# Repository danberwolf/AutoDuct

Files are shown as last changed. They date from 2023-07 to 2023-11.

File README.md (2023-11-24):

# AutoDuct: smart motorized air duct shutter
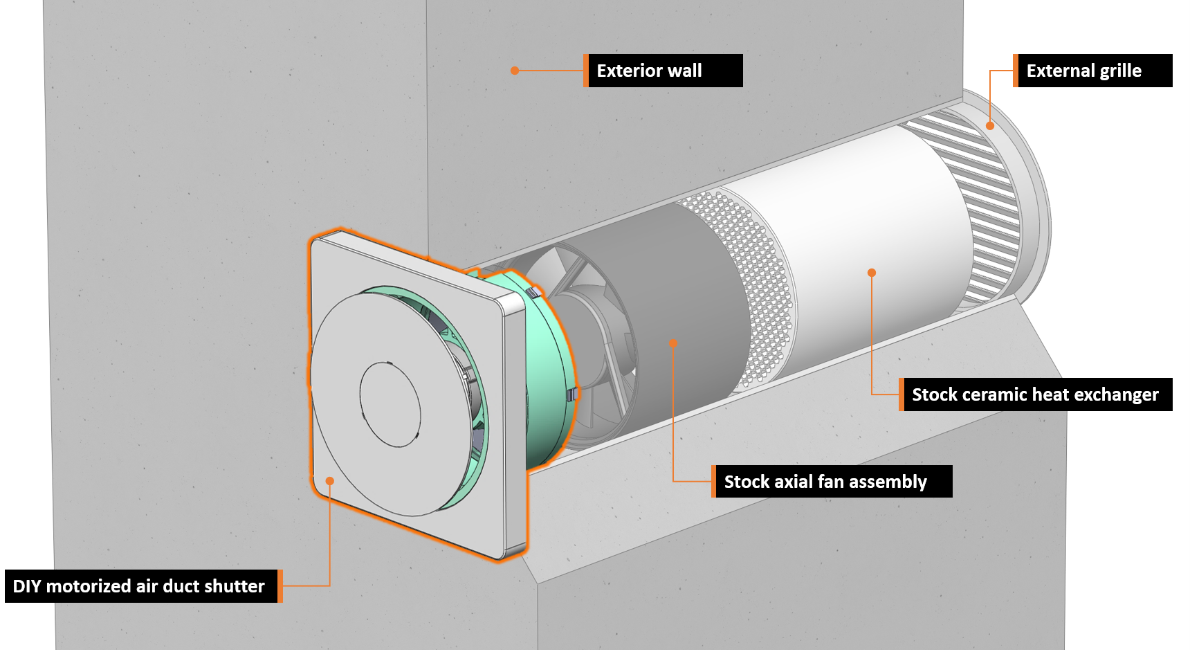
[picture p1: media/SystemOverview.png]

AutoDuct is a smart DIY air duct shutter for decentralized ventilation systems in residential buildings. Its main purpose is to automatically control airflow and block outside noise using a 3D-printed shutter system. This solves the problem of unintended air flow into the apartment during cold and windy days to increase comfort, maintain energy efficiency and reduce expenses for heating.
The integrated electronics of the air duct shutter assembly also gives full control of the ventilation system’s fan to enable features like flexible ventilation schedules and automatic humidity control. The Bluetooth low energy interface lets you control and configure the system via a mobile app. Multiple ventilation units can also be integrated into Apple HomeKit via a simple ESP32-powered BLE-to-Wifi-bridge.

# Mechanical Assembly

At the heart of this device is a mostly 3D-printed linear actuator which is used to open and close a shutter disc to prevent unwanted airflow. The 3D-printed leadscrew of the actuator is directly attached to a small brushed DC motor with an integrated gearbox.

Integrated into the encapsulated actuator unit two hall effect switches on a separate ring-shaped PCB are used to detect the end stop positions (open/close) of the shutter mechanism in combination with tiny magnets. The axial position of these magnets can be adjusted to compensate for mechanical tolerances in the assembly.

Note: the actuator unit does not use any additional (ball) bearings to keep the BOM simple and material cost low. Axial and radial forces are solely absorbed by the 3D-printed linear guides and the integrated bearings of the geared motor. This could potentially reduce longevity of the assembly but has not been an issue while testing multiple units over more than a year now. Use of silicone grease is highly recommended.



# Electronics

The electronics are based around a Microchip 32-bit microcontroller (PIC32MX), which might be a little bit overpowered for this project but was available from a previous project and has a neat footprint. The +3V3 rail is generated from the +12V bus by a step-down converter. The geared DC motor is driven by a dedicated H-bridge driver IC (DRV8801).

Behind the front cover of the assembly another small PCB is hidden. This PCB contains the Bluetooth low energy module (HM-17), a serial EEPROM, a real time clock (RTC) IC and a humidity and temperature sensor. User feedback is given via a white LED which shines through the 3D-printed enclosure and has brightness control via PWM.

# Firmware

The main processor of the device (PIC32MX150F128B) runs a super simple multitasking OS which takes care of these main tasks:

* monitoring of fan control PWM signal from the stock ventilation system control bus
* reading of temperature / humidity from SHT31 sensor
* generating the PWM control signal for connected fan
* motor control including end stop detection
* handle the BLE communication when the system is connected to the mobile app 

Depending on the selected operating mode, the device will perform the following actions:

* opening / closing the valve based on the detected fan control PWM signal
* automatically activating the fan based on schedule events or humidity thresholds
* react to remote control commands issued via the mobile app / BLE connection 

A custom bootloader was developed which enables over-the-air firmware updates via the Bluetooth low energy interface. 

# Project Video
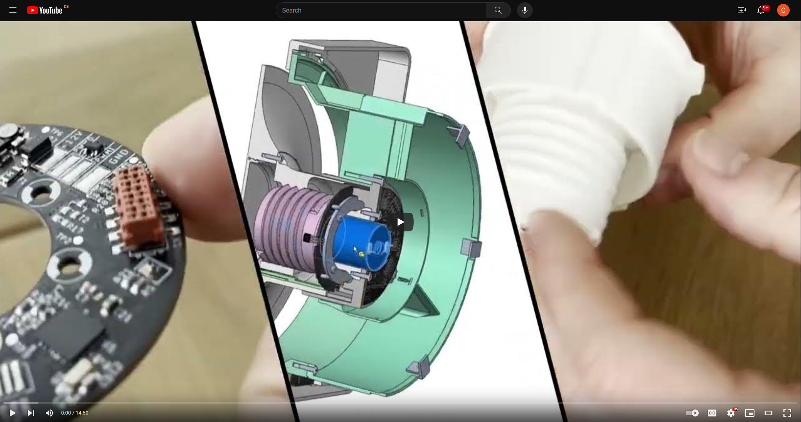
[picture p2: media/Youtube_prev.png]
Watch the video (https://youtu.be/yPaX_Ez_lKY)


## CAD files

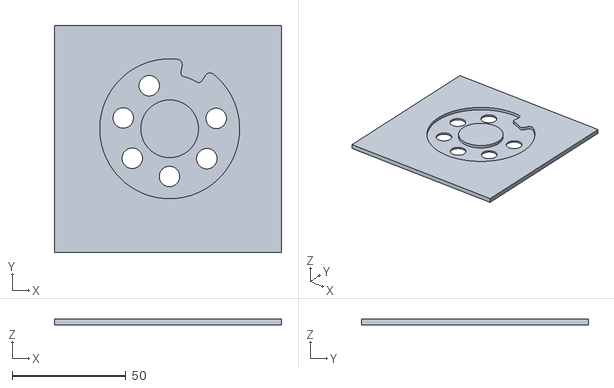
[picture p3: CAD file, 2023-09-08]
CAD/PCBassemblyTemplate.STL
100.0 x 100.0 x 2.50

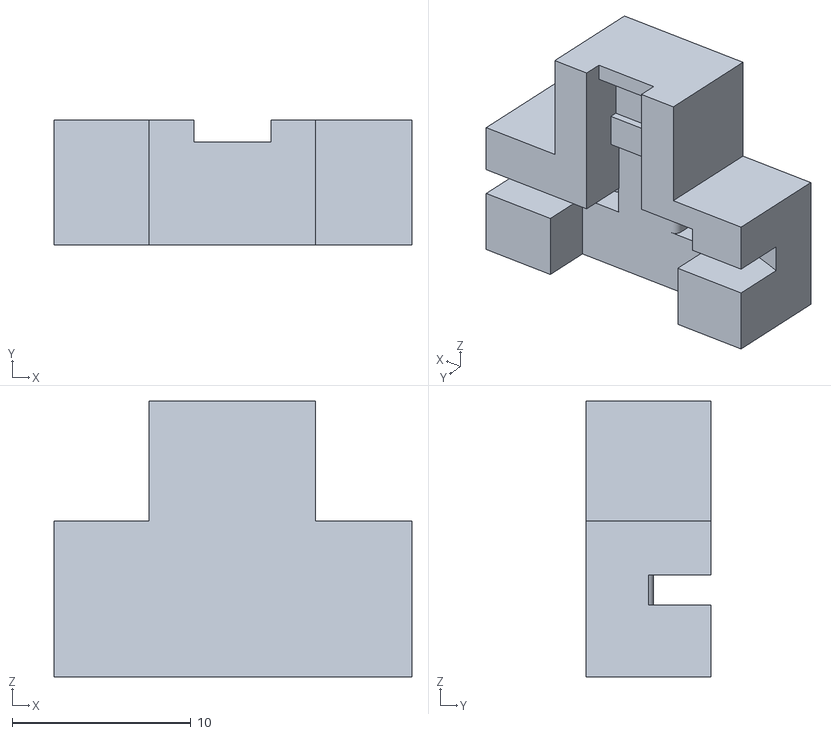
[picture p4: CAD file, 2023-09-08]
CAD/SensorAlignmentTemplate.STL
20.0 x 7.00 x 15.4

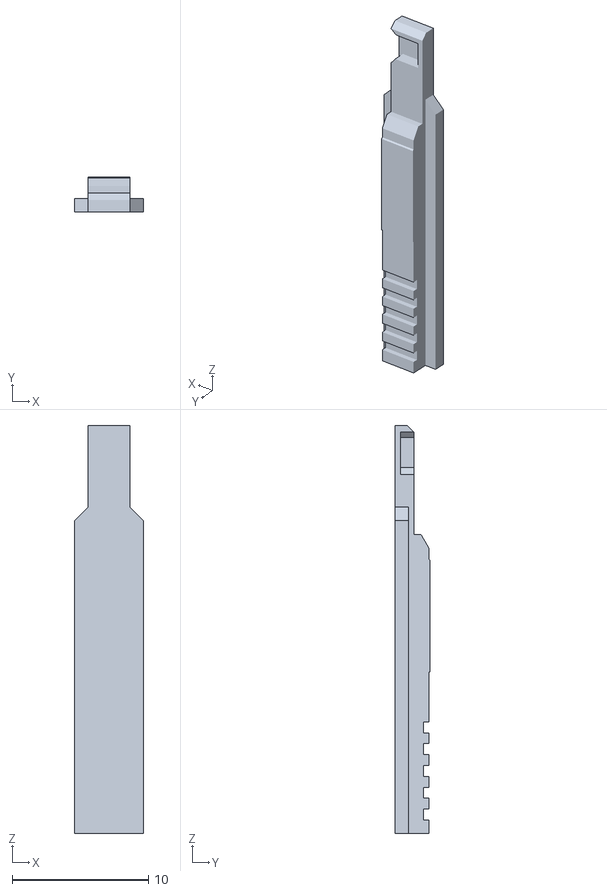
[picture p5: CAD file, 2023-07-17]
CAD/MagnetCarrierShort.STL
5.10 x 2.60 x 30.0

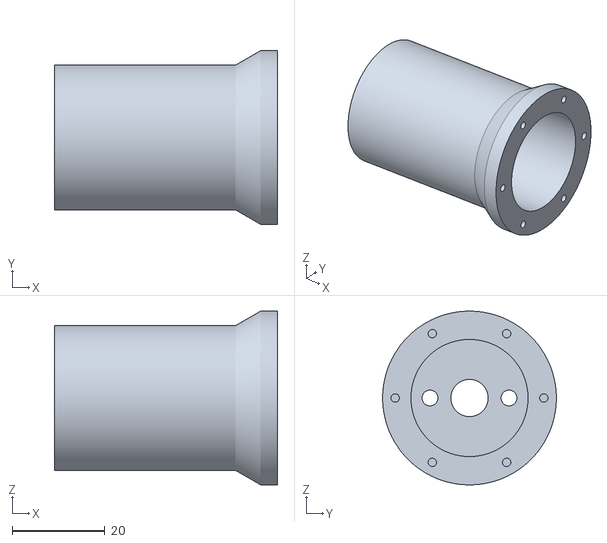
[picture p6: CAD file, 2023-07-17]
CAD/MotorCarrier.STL
48.0 x 37.4 x 37.4

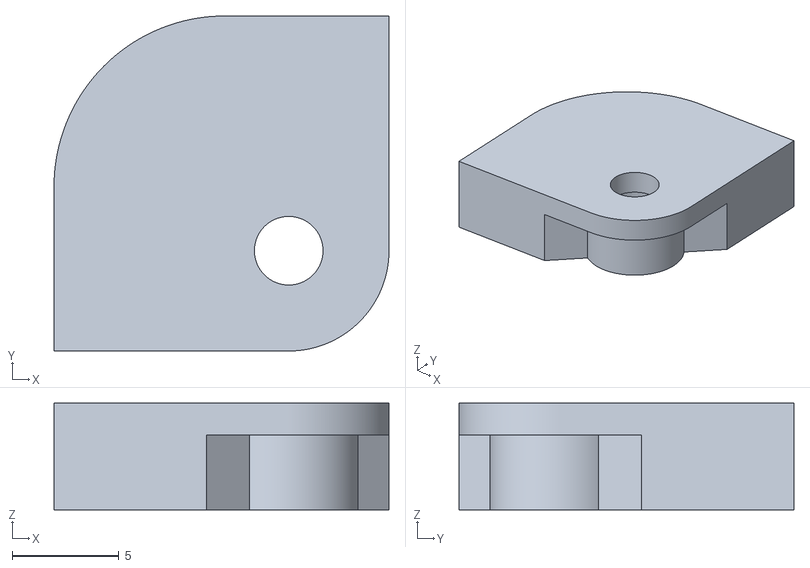
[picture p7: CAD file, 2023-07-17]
CAD/SensorCover.STL
15.7 x 15.7 x 5.00

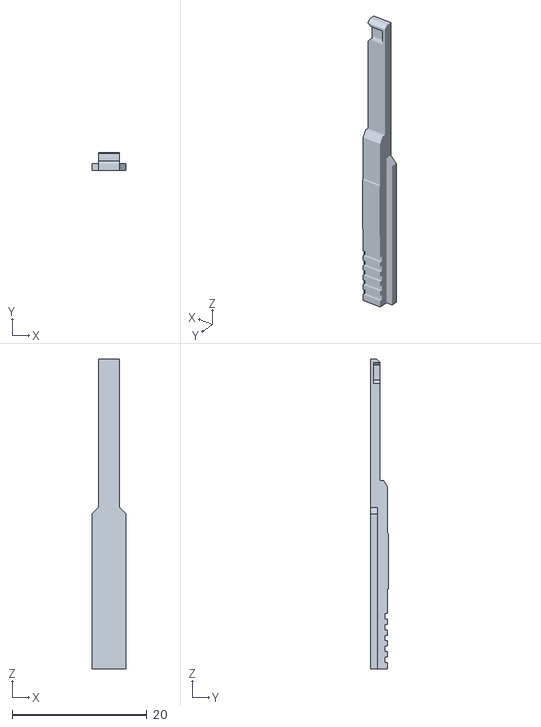
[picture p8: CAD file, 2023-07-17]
CAD/MagnetCarrierLong.STL
5.10 x 2.60 x 46.0

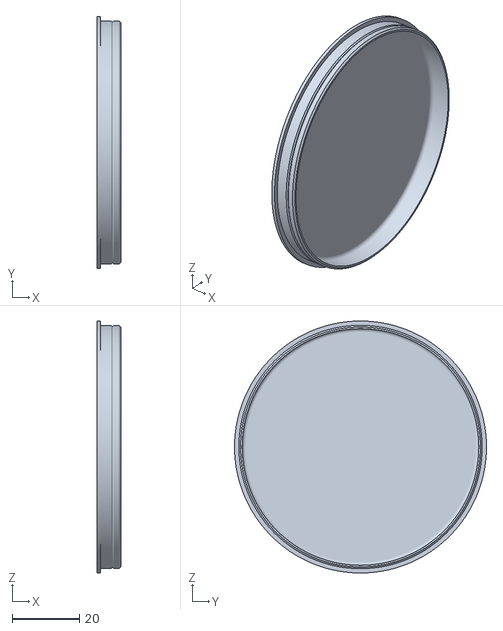
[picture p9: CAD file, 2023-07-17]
CAD/FlatCap.STL
7.00 x 75.0 x 75.0

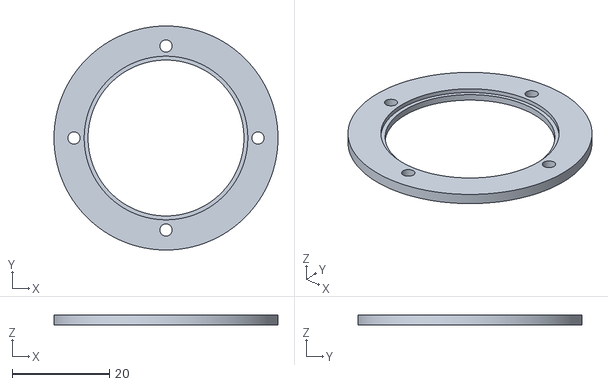
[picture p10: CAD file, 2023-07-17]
CAD/ThrustRing.STL
46.0 x 46.0 x 2.00

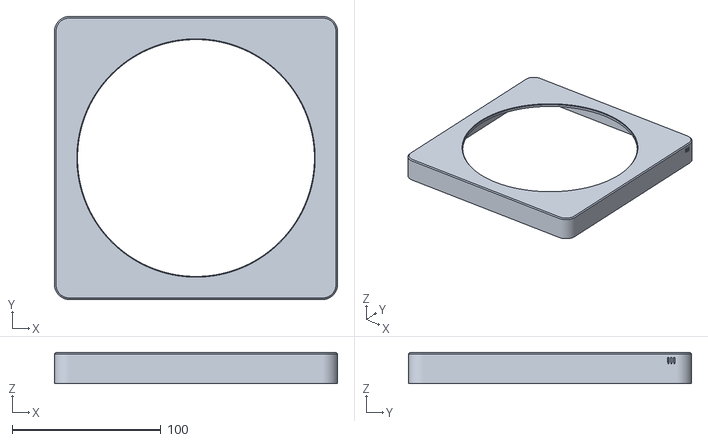
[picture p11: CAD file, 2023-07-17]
CAD/VentCover.STL
190.0 x 190.0 x 21.0

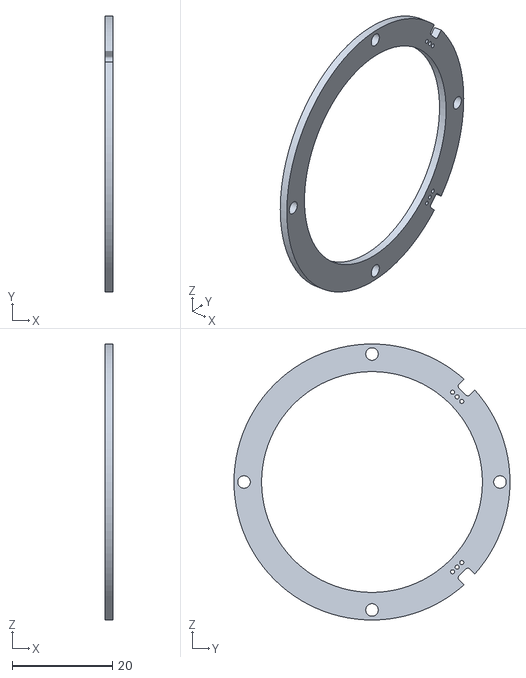
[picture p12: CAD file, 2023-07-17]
CAD/ThrustCollar.STL
1.60 x 55.0 x 55.0

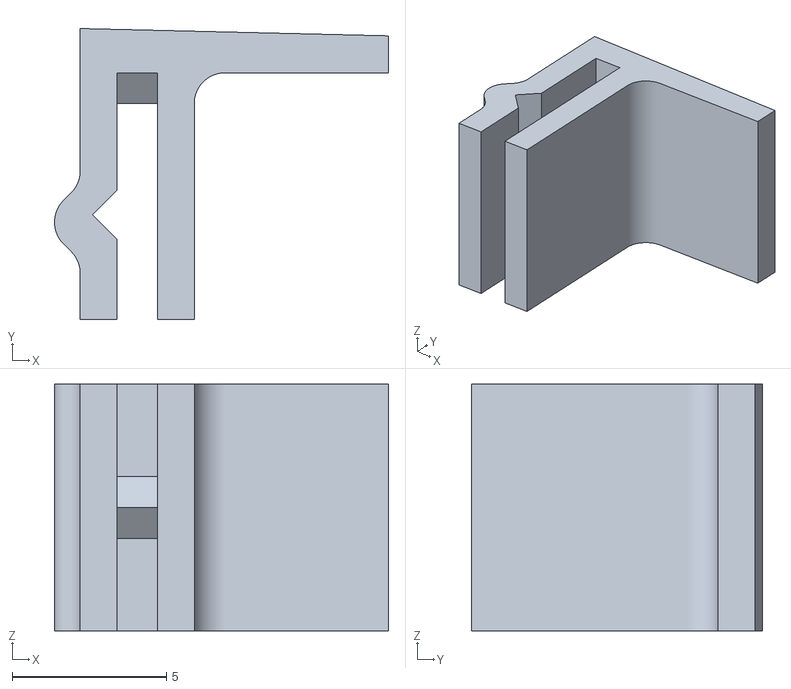
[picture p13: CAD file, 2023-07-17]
CAD/FilterClamp.STL
10.8 x 9.44 x 8.00

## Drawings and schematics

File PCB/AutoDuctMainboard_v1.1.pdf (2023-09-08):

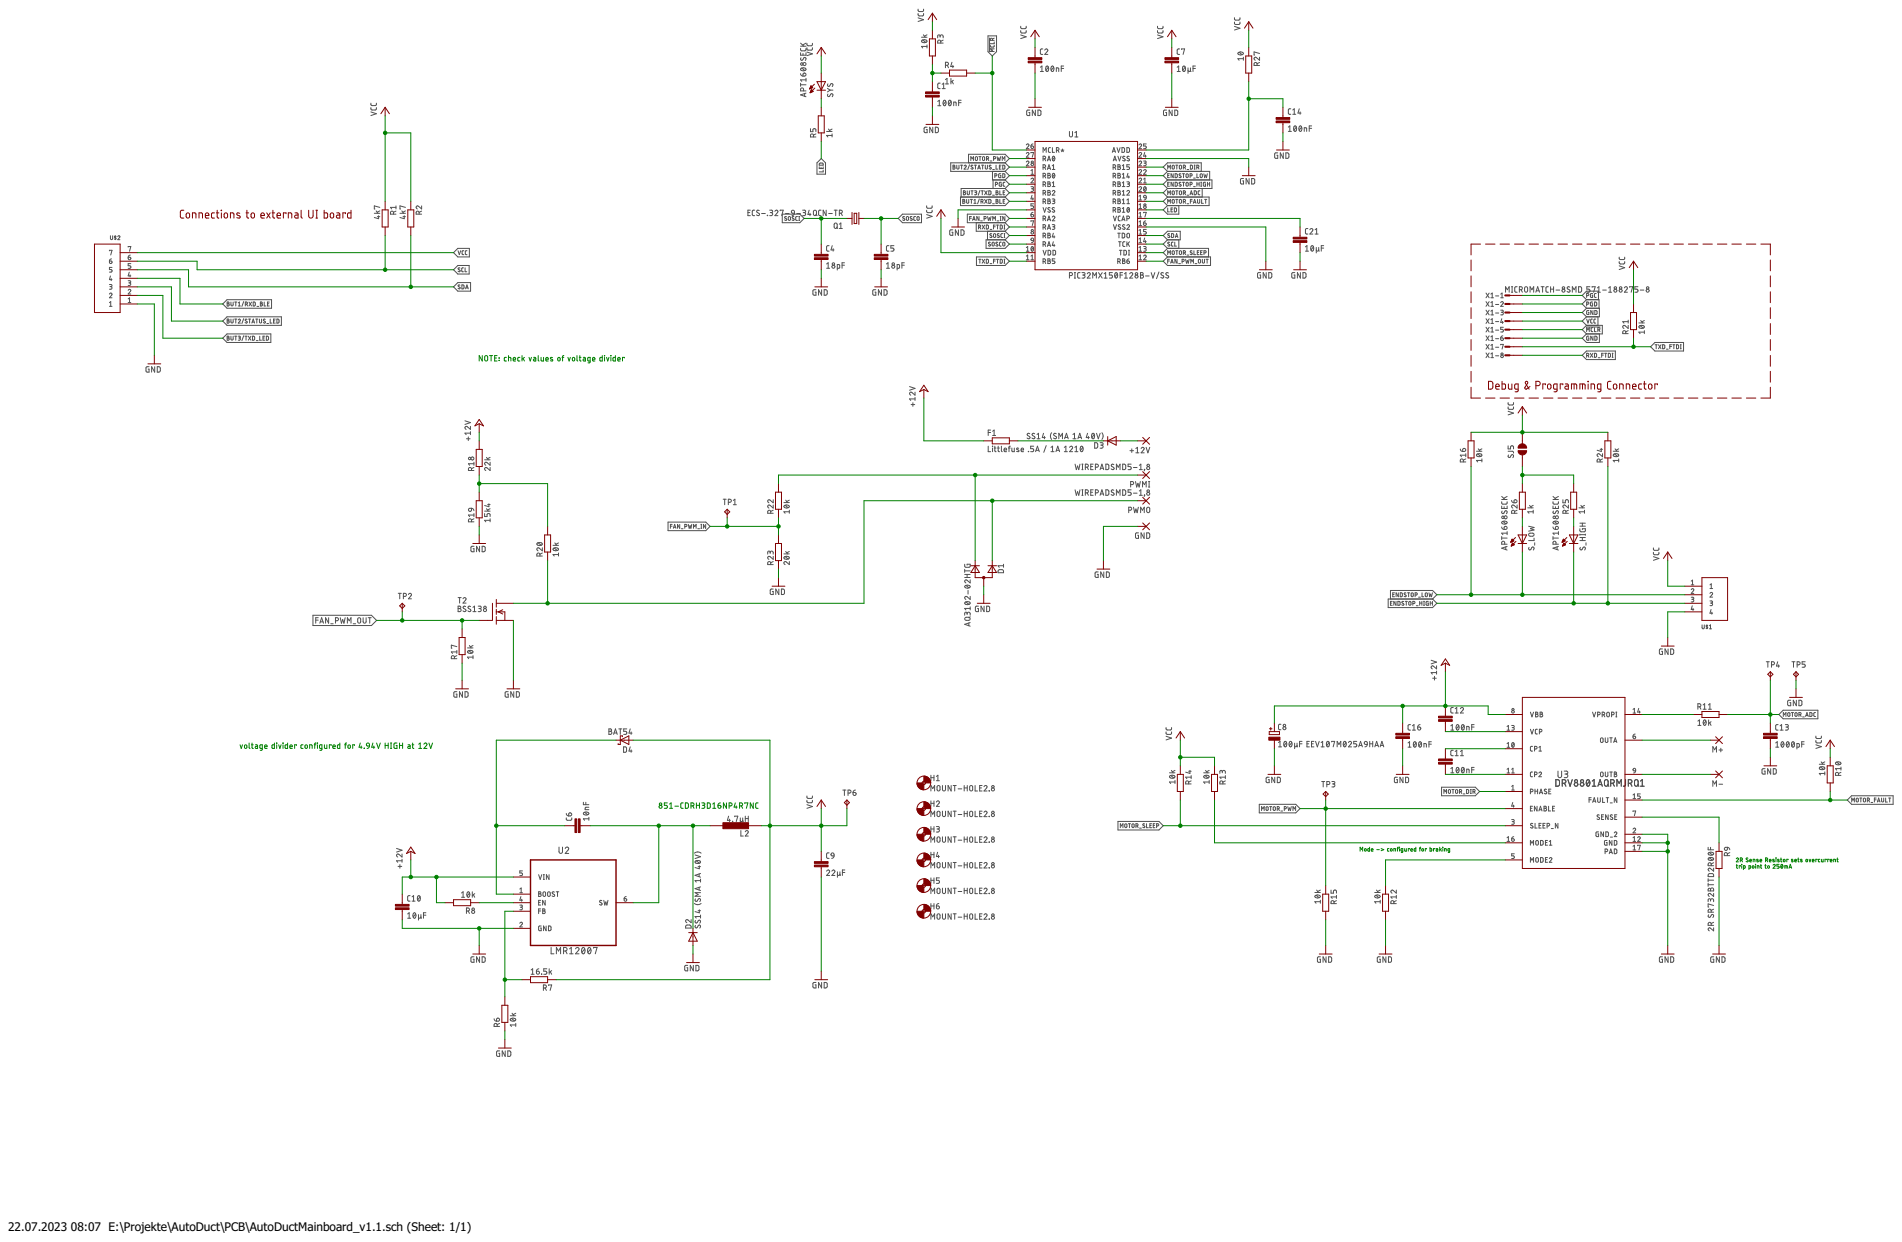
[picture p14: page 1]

22.07.2023 08:07 E:\Projekte\AutoDuct\PCB\AutoDuctMainboard_v1.1.sch (Sheet: 1/1)

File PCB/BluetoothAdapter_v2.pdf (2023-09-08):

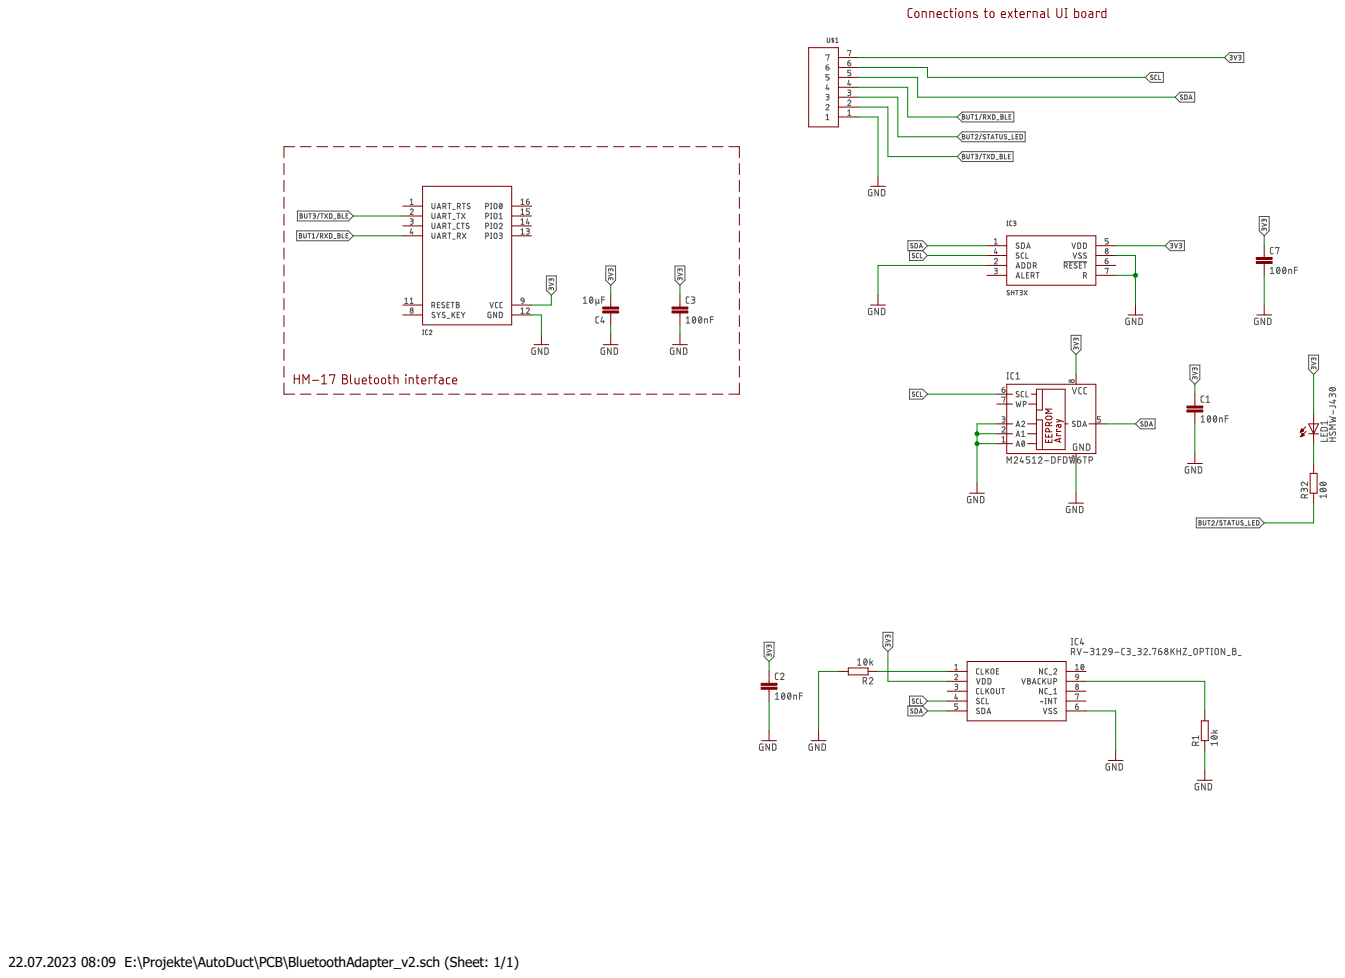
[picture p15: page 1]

22.07.2023 08:09 E:\Projekte\AutoDuct\PCB\BluetoothAdapter_v2.sch (Sheet: 1/1)

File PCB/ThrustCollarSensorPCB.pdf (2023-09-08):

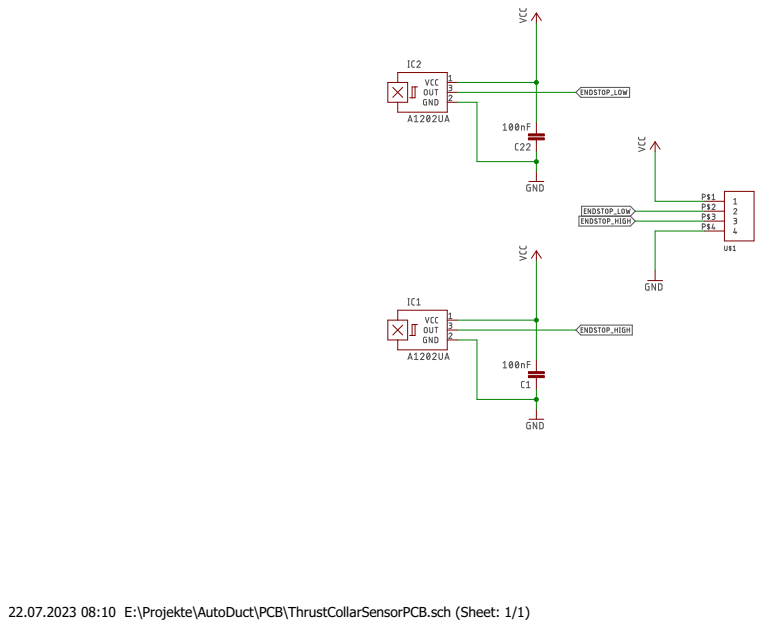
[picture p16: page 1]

22.07.2023 08:10 E:\Projekte\AutoDuct\PCB\ThrustCollarSensorPCB.sch (Sheet: 1/1)

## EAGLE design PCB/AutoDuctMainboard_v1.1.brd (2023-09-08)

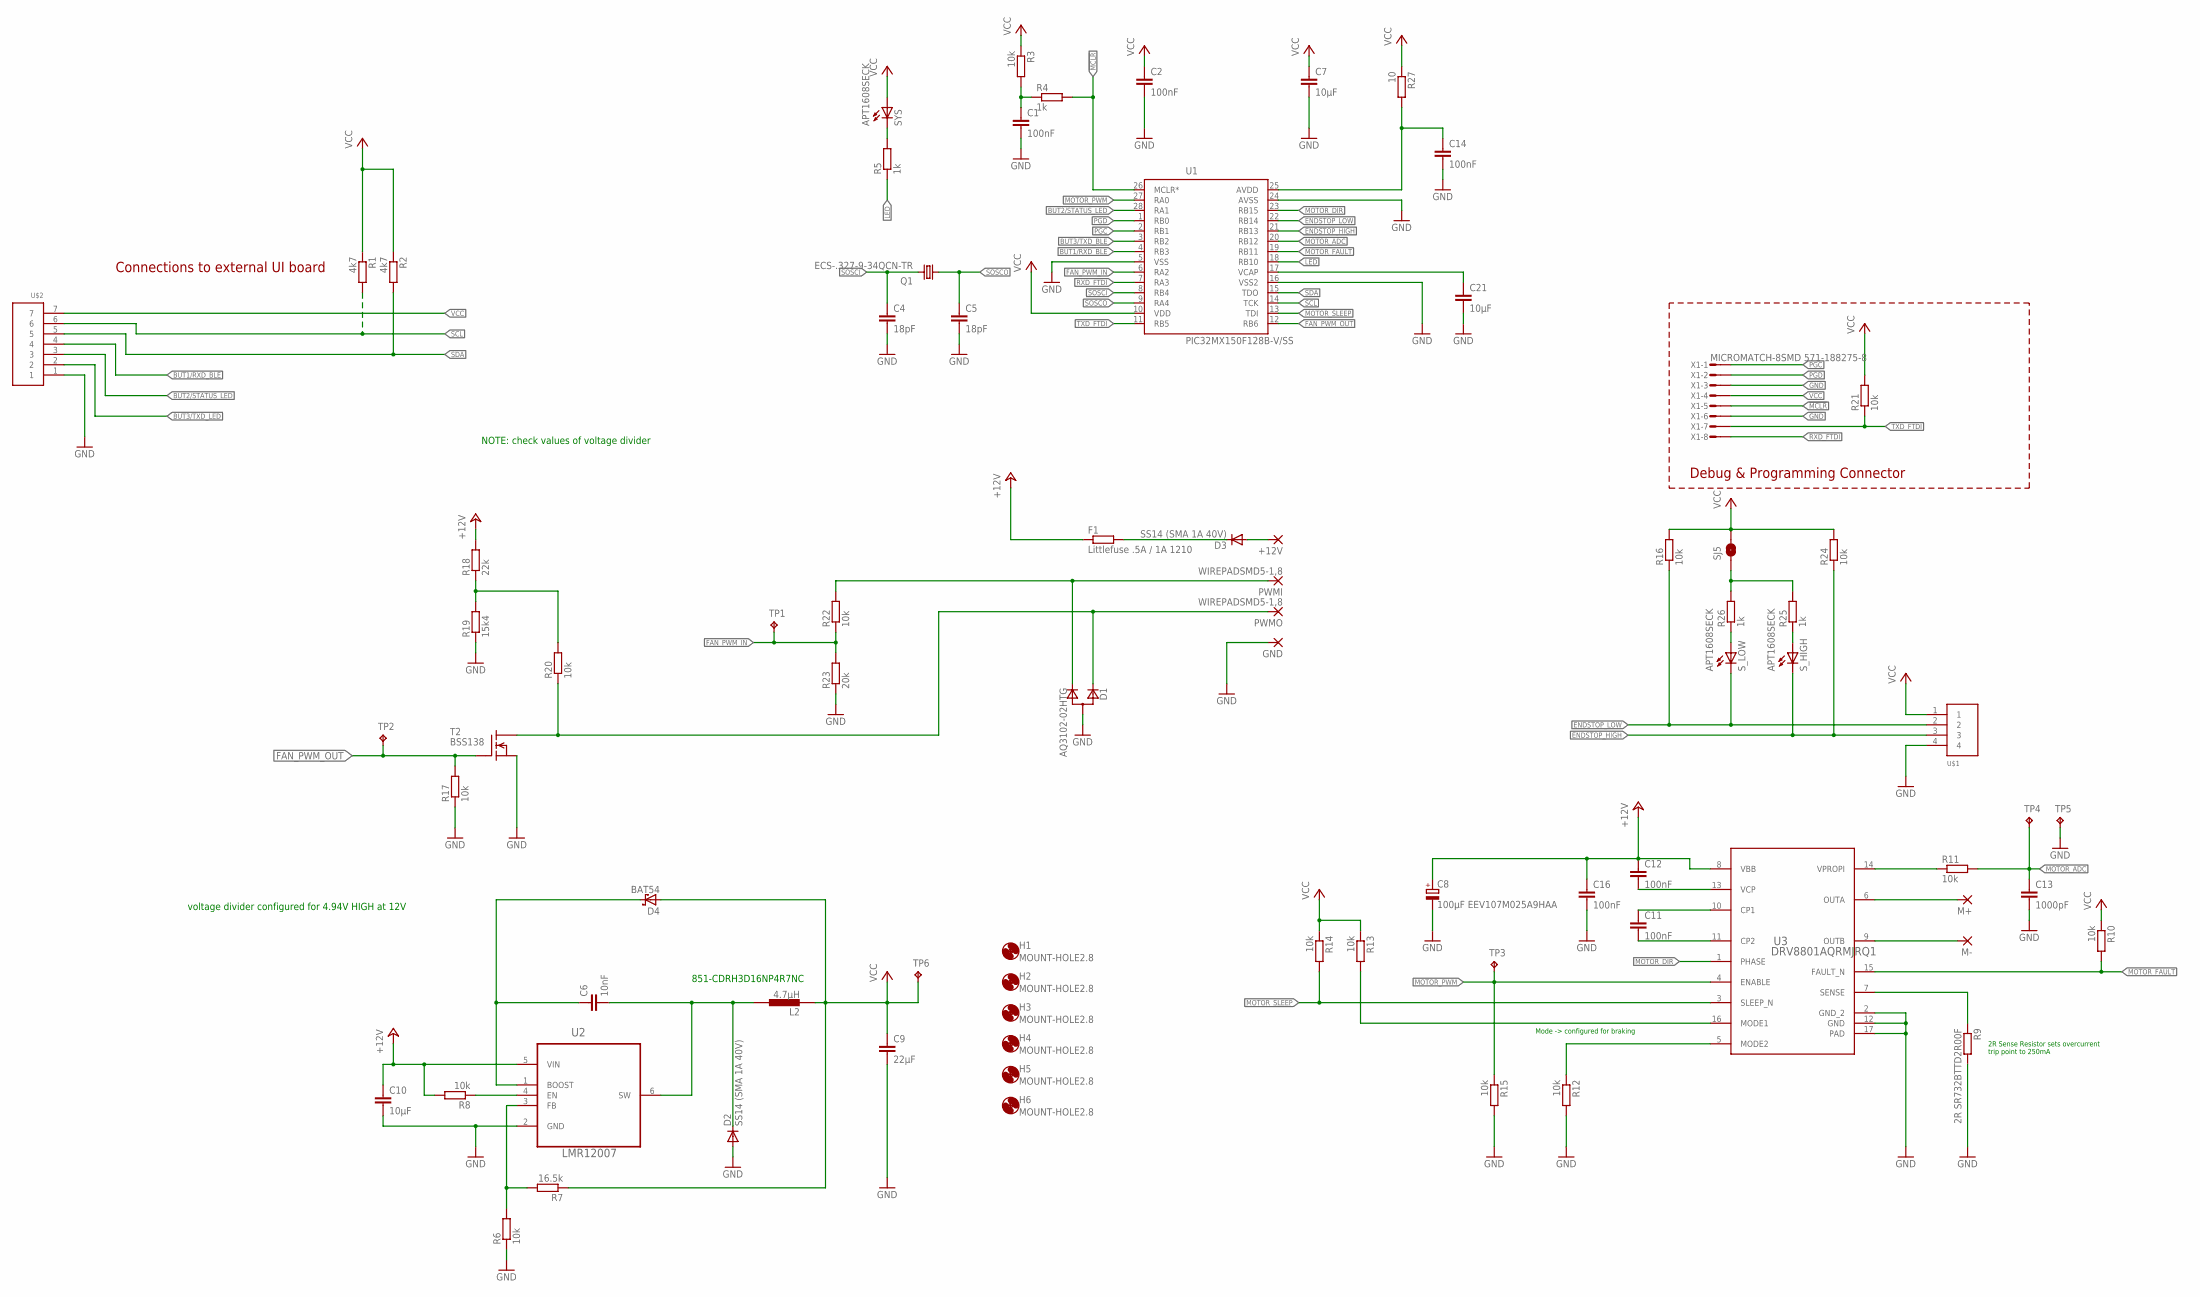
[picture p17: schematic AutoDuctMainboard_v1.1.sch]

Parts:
+12V: SMD5; SMD2,54-5,08
C1, C2, C11, C12, C14: 100nF; C0402
C4, C5: 18pF; C0603K
C6: 10nF; C0603K
C7, C21: 10µF; C0603K
C8: 100µF EEV107M025A9HAA; 153CLV-0605
C9: 22µF; C0805K
C10: 10µF; C1206K
C13: 1000pF; C0603K
C16: 100nF; C0603K
D1: AQ3102-02HTG; SOT323
D2, D3: SS14 (SMA 1A 40V); DO214AC
D4: BAT54; SOT23
F1: Littlefuse .5A / 1A 1210; R1210
GND: SMD5; SMD2,54-5,08
H1, H2, H3, H4, H5, H6: MOUNT-HOLE2.8; 2,8
L2: 4.7µH; CDRH3D16; MOUSER CDRH3D16/LDNP-4R7NC
M+: SMD5; SMD2,54-5,08
M-: SMD5; SMD2,54-5,08
PWMI: WIREPADSMD5-1,8; 5-1,8
PWMO: WIREPADSMD5-1,8; 5-1,8
Q1: ECS-.327-9-34QCN-TR; 3.2X1.5
R1, R2: 4k7; R0603
R3, R6, R8, R10, R11, R12, R13, R14, R15, R16, R17, R20, R21, R22, R24: 10k; R0603
R4, R5, R25, R26: 1k; R0603
R7: 16.5k; R0603
R9: 2R SR732BTTD2R00F; R1206
R18: 22k; R0603
R19: 15k4; R0603
R23: 20k; R0603
R27: 10; R0603
SJ5: RXLED; SJ_2S-NO
SYS: APT1608SECK; CHIPLED_0603
S_HIGH: APT1608SECK; CHIPLED_0603
S_LOW: APT1608SECK; CHIPLED_0603
T2: BSS138; SOT23
TP1, TP2, TP3, TP6: TPTP13R; TP13R
TP4: TPTP09R; TP09R
TP5: TPTP12SQ; TP12SQ
U1: PIC32MX150F128B-V/SS; QFN65P600X600X100-29N
U2: LMR12007; SOT95P285X100-6N
U3: DRV8801AQRMJRQ1; RMJ0016A
U$1: WIREPAD1X4
U$2: WIREPAD1X7
X1: MICROMATCH-8SMD 571-188275-8; MICROMATCH-8-SMD

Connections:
!MCLR: R4.2, U1.26 (MCLR*), X1.5
+12V: C8.+, C10.1, C12.1, C16.1, F1.1, R8.2, R18.2, U2.5 (VIN), U3.8 (VBB)
BUT1/RXD_BLE: U1.4 (RB3), U$2.4
BUT2/STATUS_LED: U1.28 (RA1), U$2.3
BUT3/TXD_BLE: U1.3 (RB2)
BUT3/TXD_LED: U$2.2
ENDSTOP_HIGH: R24.1, S_HIGH.C, U1.21 (RB13), U$1.3
ENDSTOP_LOW: R16.1, S_LOW.C, U1.22 (RB14), U$1.2
FAN_PWM_IN: R22.1, R23.2, TP1.TP, U1.6 (RA2)
FAN_PWM_IN_RAW: D1.3 (C2), PWMI.1, R22.2
FAN_PWM_OUT: R17.2, T2.1 (G), TP2.TP, U1.12 (RB6)
FAN_PWM_OUT_SHIFTED: D1.2 (C1), PWMO.1, R20.1, T2.3 (D)
GND: C1.2, C2.2, C4.2, C5.2, C7.2, C8.-, C9.2, C10.2, C13.2, C14.2, C16.2, C21.2, D1.1 (A), D2.A, GND.1, R6.1, R9.2, R12.2, R15.2, R17.1, R19.1, R23.1, T2.2 (S), TP5.TP, U1.5 (VSS), U1.16 (VSS2), U1.24 (AVSS), U2.2 (GND), U3.2 (GND_2), U3.12 (GND), U3.17 (PAD), U$1.4, U$2.1, X1.3, X1.6
LED: R5.1, U1.18 (RB10)
MOTOR+: M+.1, U3.6 (OUTA)
MOTOR-: M-.1, U3.9 (OUTB)
MOTOR_ADC: C13.1, R11.2, TP4.TP, U1.20 (RB12)
MOTOR_DIR: U1.23 (RB15), U3.1 (PHASE)
MOTOR_FAULT: R10.2, U1.19 (RB11), U3.15 (FAULT_N)
MOTOR_PWM: R15.1, TP3.TP, U1.27 (RA0), U3.4 (ENABLE)
MOTOR_SLEEP: R14.2, U1.13 (TDI), U3.3 (SLEEP_N)
unnamed: R5.2, SYS.C
unnamed: C1.1, R3.2, R4.1
unnamed: R8.1, U2.4 (EN)
unnamed: C11.1, U3.10 (CP1)
unnamed: +12V.1, D3.A
unnamed: C11.2, U3.11 (CP2)
unnamed: C6.1, D4.3 (C), U2.1 (BOOST)
unnamed: C12.2, U3.13 (VCP)
unnamed: R6.2, R7.2, U2.3 (FB)
unnamed: C6.2, D2.C, L2.2, U2.6 (SW)
unnamed: R13.2, U3.16 (MODE1)
unnamed: R12.1, U3.5 (MODE2)
unnamed: R25.2, R26.2, SJ5.1
unnamed: R9.1, U3.7 (SENSE)
unnamed: R26.1, S_LOW.A
unnamed: D3.C, F1.2
unnamed: R18.1, R19.2, R20.2
unnamed: R11.1, U3.14 (VPROPI)
unnamed: R25.1, S_HIGH.A
unnamed: C14.1, R27.2, U1.25 (AVDD)
PGC: U1.2 (RB1), X1.1
PGD: U1.1 (RB0), X1.2
RXD_FTDI: U1.7 (RA3), X1.8
SCL: R1.2, U1.14 (TCK), U$2.6
SDA: R2.2, U1.15 (TDO), U$2.5
SOSCI: C4.1, Q1.2, U1.8 (RB4)
SOSCO: C5.1, Q1.1, U1.9 (RA4)
TXD_FTDI: R21.1, U1.11 (RB5), X1.7
VCAP: C21.1, U1.17 (VCAP)
VCC: C2.1, C7.1, C9.1, D4.1 (A), L2.1, R1.1, R2.1, R3.1, R7.1, R10.1, R13.1, R14.1, R16.2, R21.2, R24.2, R27.1, SJ5.2, SYS.A, TP6.TP, U1.10 (VDD), U$1.1, U$2.7, X1.4

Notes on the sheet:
Connections to external UI board
Debug & Programming Connector
851-CDRH3D16NP4R7NC
2R Sense Resistor sets overcurrent trip point to 250mA
Mode -> configured for braking
voltage divider configured for 4.94V HIGH at 12V
NOTE: check values of voltage divider

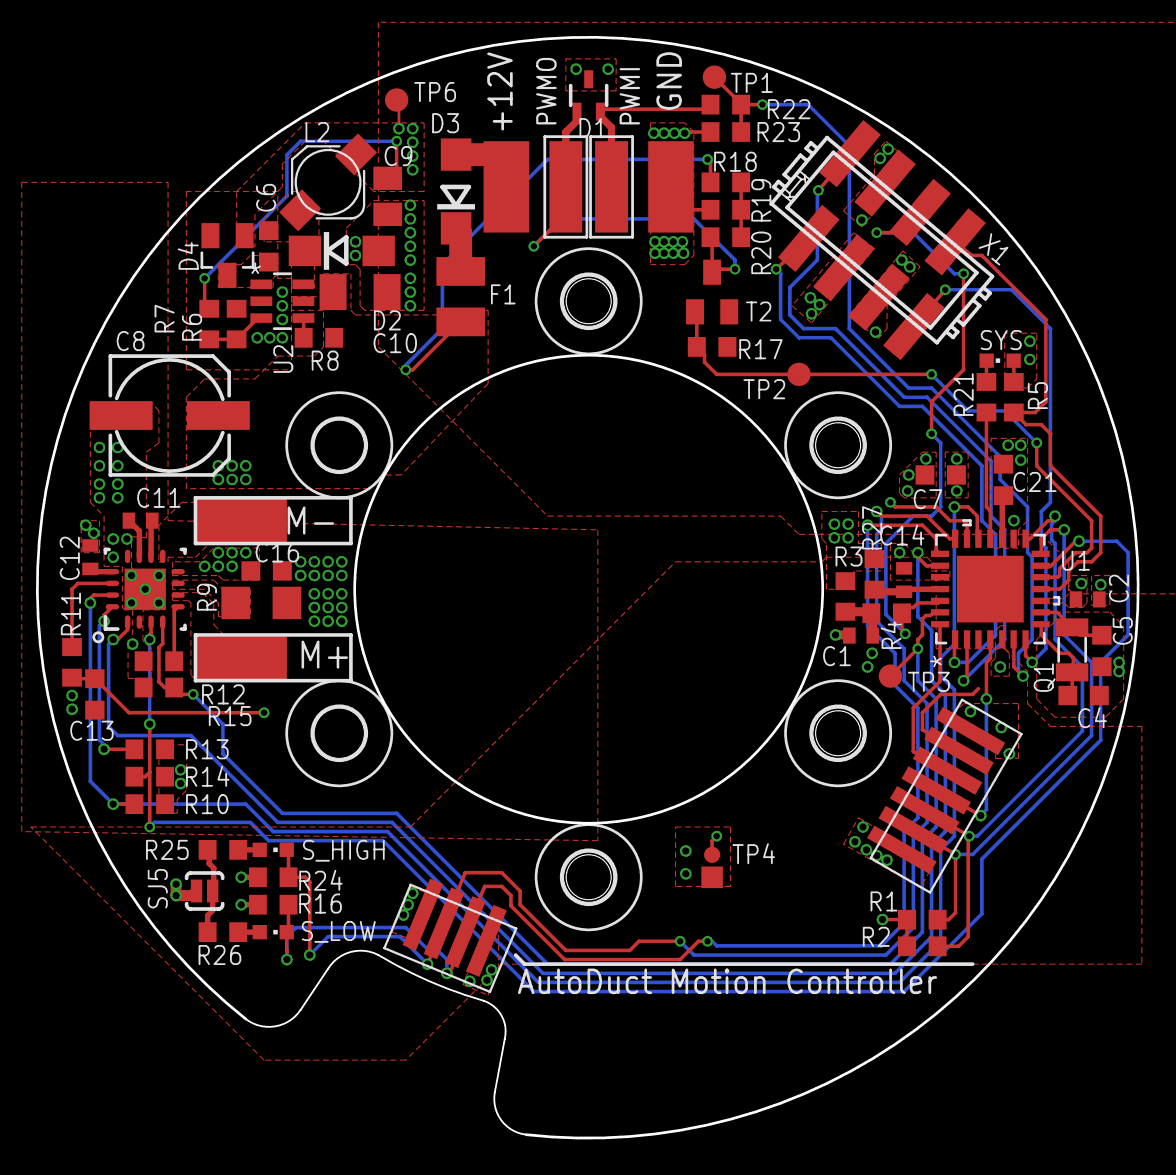
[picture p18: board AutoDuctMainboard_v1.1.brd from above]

Board: 4 copper layers, 61.2 x 61.1 mm, 78 parts (0 on the bottom side), 49 nets.

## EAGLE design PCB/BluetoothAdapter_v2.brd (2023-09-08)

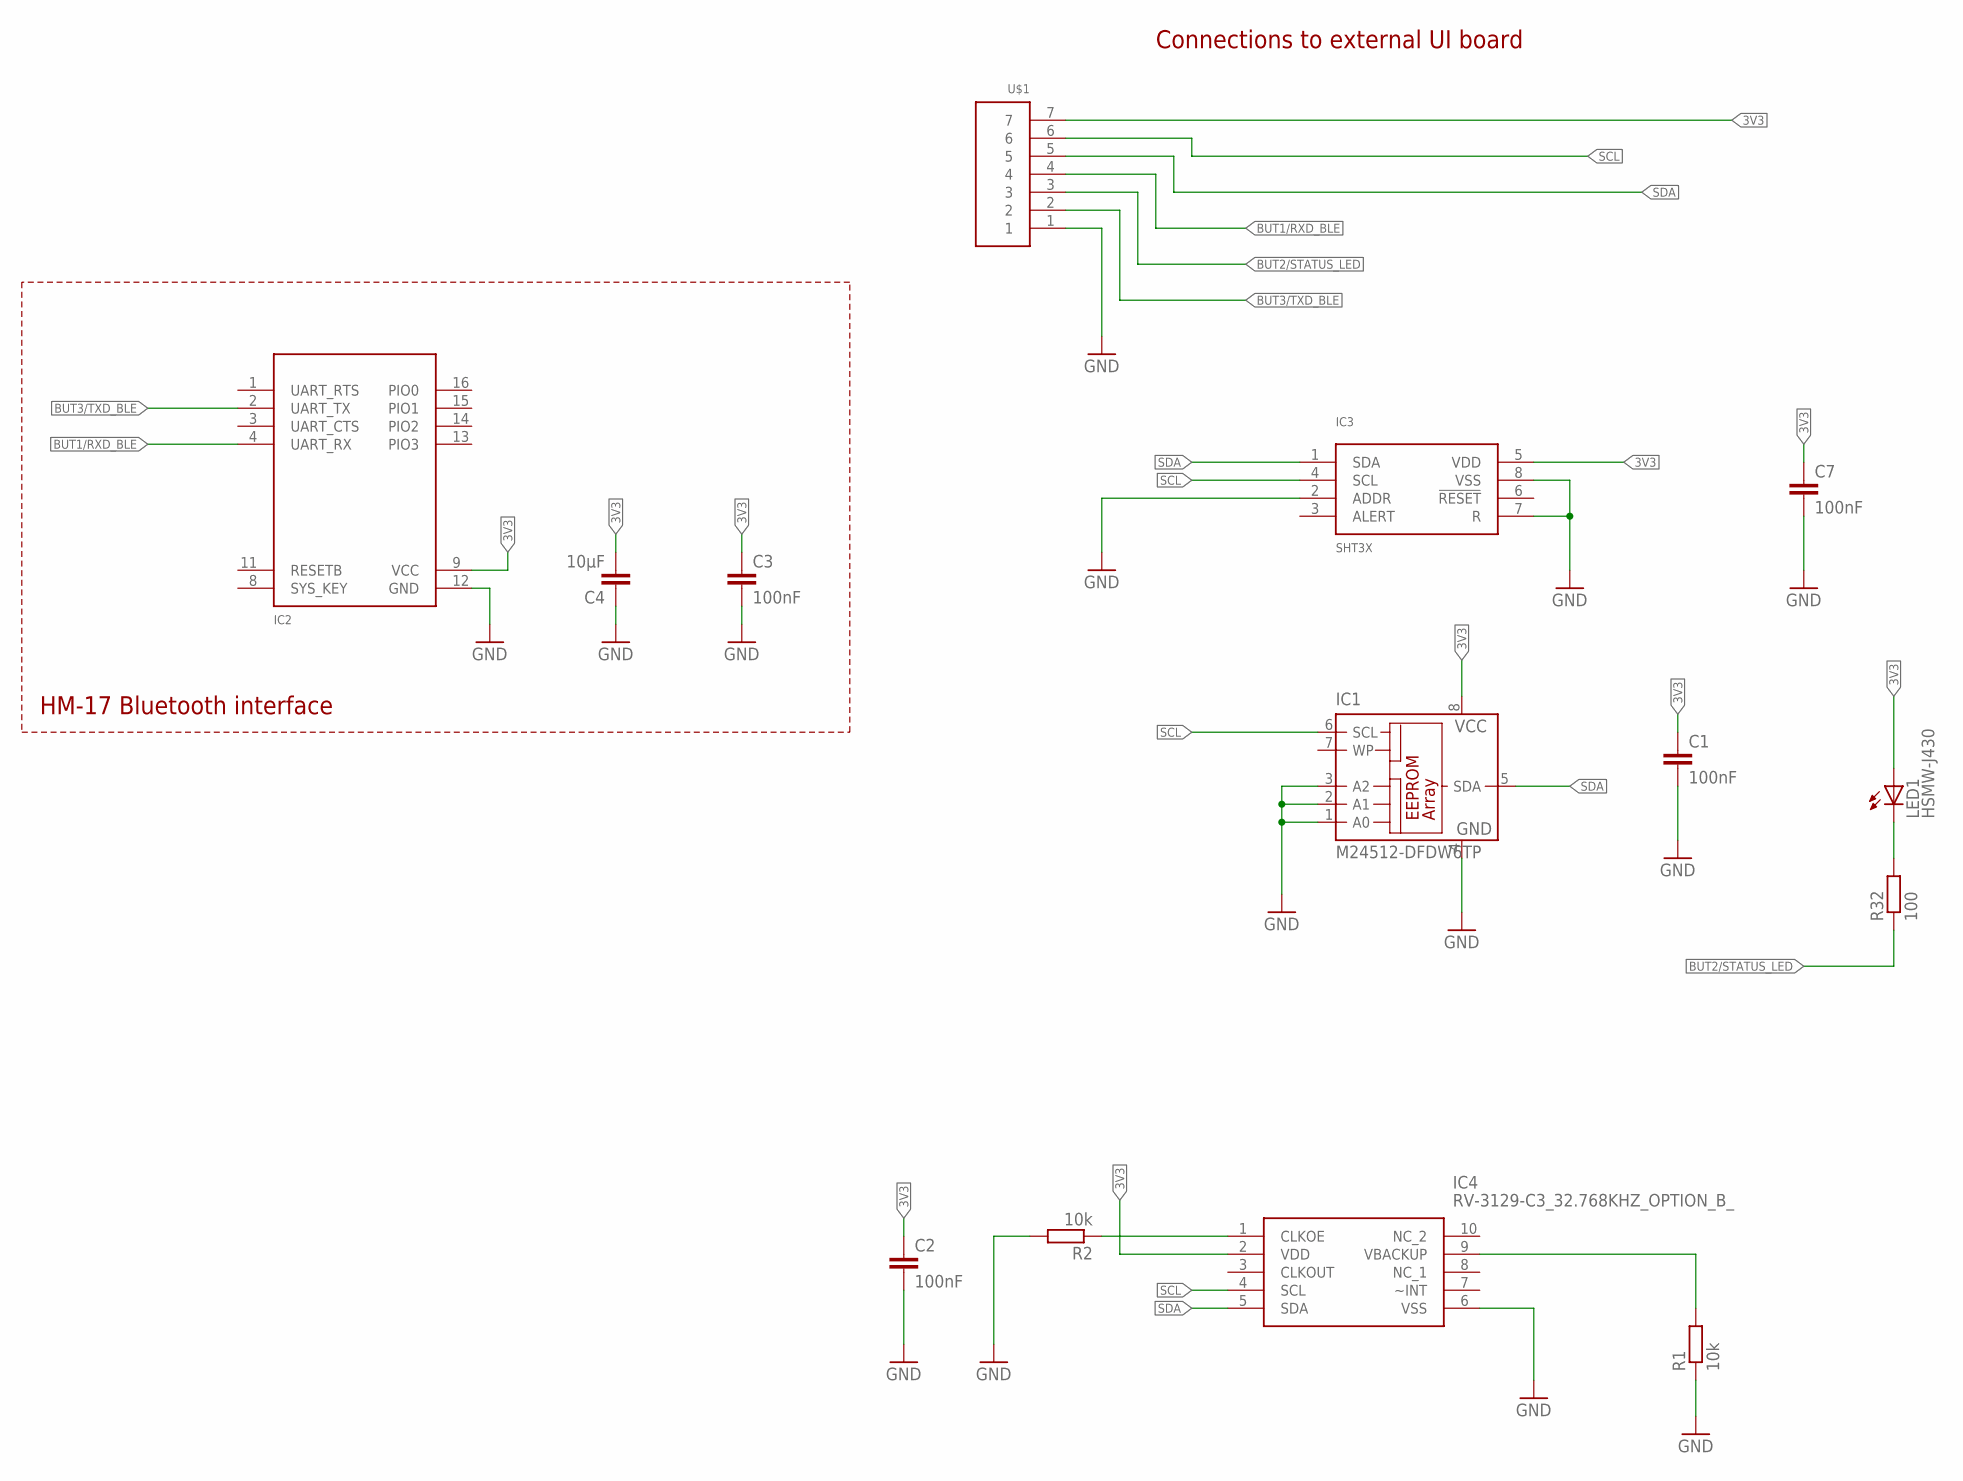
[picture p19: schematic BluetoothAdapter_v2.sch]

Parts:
C1, C2, C3, C7: 100nF; C0402
C4: 10µF; C0805K
IC1: M24512-DFDW6TP; TSSOP8
IC2: HM17
IC3: SHT3X; TDFN8-2.5X2.5MM
IC4: RV-3129-C3_32.768KHZ_OPTION_B_; RV3129C3
LED1: HSMW-J430; 1206
R1, R2: 10k; R0603
R32: 100; R0603
U$1: WIREPAD1X7

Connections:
3V3: C1.1, C2.1, C3.1, C4.2, C7.1, IC1.8 (VCC), IC2.9 (VCC), IC3.5 (VDD), IC4.2 (VDD), LED1.A, U$1.7
BUT1/RXD_BLE: IC2.4 (UART_RX), U$1.4
BUT2/STATUS_LED: R32.1, U$1.3
BUT3/TXD_BLE: IC2.2 (UART_TX), U$1.2
GND: C1.2, C2.2, C3.2, C4.1, C7.2, IC1.1 (A0), IC1.2 (A1), IC1.3 (A2), IC1.4 (GND), IC2.12 (GND), IC3.2 (ADDR), IC3.7 (R), IC3.8 (VSS), IC4.6 (VSS), R1.1, R2.2, U$1.1
unnamed: IC4.9 (VBACKUP), R1.2
unnamed: LED1.C, R32.2
unnamed: IC4.1 (CLKOE), R2.1
SCL: IC1.6 (SCL), IC3.4 (SCL), IC4.4 (SCL), U$1.6
SDA: IC1.5 (SDA), IC3.1 (SDA), IC4.5 (SDA), U$1.5

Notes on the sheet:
HM-17 Bluetooth interface
Connections to external UI board

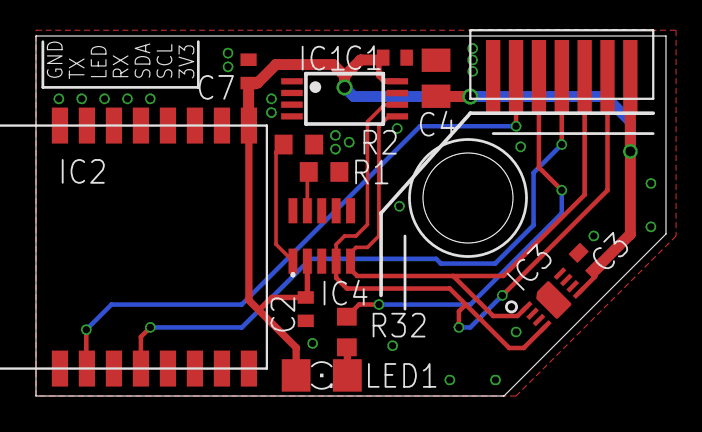
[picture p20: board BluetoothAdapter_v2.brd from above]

Board: 2 copper layers, 35.0 x 20.0 mm, 14 parts (0 on the bottom side), 10 nets.

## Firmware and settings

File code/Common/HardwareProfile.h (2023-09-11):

// AutoDuct Hardware definition file
// (C) 2023-09-09 by Daniel Porzig

#ifndef HARDWARE_PROFILE_H
#define HARDWARE_PROFILE_H


#include "Compiler.h"

   /** CPU Clock Speed Assignment *************************************/
    
	#define GetSystemClock()		(40000000ul)      // Hz
//	#define GetSystemClock()		(48000000ul)      // Hz
	#define GetInstructionClock()	(GetSystemClock())
	#define GetPeripheralClock()	(GetInstructionClock() / 1)	// Set your divider according to your Peripheral Bus Frequency configuration fuse setting



// ====================================================
//   Hardware mappings
// ====================================================

// BDC Motor Driver
#define MOTOR_DIR_TRIS      (TRISBbits.TRISB15)
#define MOTOR_DIR           (LATBbits.LATB15)

#define MOTOR_PWM_TRIS      (TRISAbits.TRISA0)
#define MOTOR_PWM           (LATAbits.LATA0)


#define MOTOR_SLEEP_TRIS    (TRISBbits.TRISB7)
#define MOTOR_SLEEP         (LATBbits.LATB7)

#define MOTOR_FAULT_TRIS    (TRISBbits.TRISB11)
#define MOTOR_FAULT         (LATBbits.LATB11)

#define MOTOR_ADC_TRIS      (TRISBbits.TRISB12)

// % LED INDICATORS										
#define SYSLED_TRIS         (TRISBbits.TRISB10)
#define SYSLED              (LATBbits.LATB10)

#define STATLED_TRIS         (TRISAbits.TRISA1)
#define STATLED              (LATAbits.LATA1)


//UART 2   - DEBUG
#define 	RX_CON_TRIS		(TRISBbits.TRISB5)      // input (RX)
#define 	TX_CON_TRIS		(TRISAbits.TRISA3)      // output (TX)

//UART 1   - HM-17
#define 	RX_BLE_TRIS		(TRISBbits.TRISB2)      // input (RX)
#define 	TX_BLE_TRIS		(TRISBbits.TRISB3)      // output (TX)


// PWM in/out
#define 	FAN_PWM_IN_TRIS		(TRISAbits.TRISA2)
#define 	FAN_PWM_OUT_TRIS	(TRISBbits.TRISB6)
#define 	FAN_PWM_OUT_ODC     (ODCBbits.ODCB6)      // open drain config


// user buttons
#define 	BUTTON1_TRIS		(TRISBbits.TRISB3)
#define 	BUTTON1             (PORTBbits.RB3)
        
#define 	BUTTON2_TRIS		(TRISAbits.TRISA1)
#define 	BUTTON2             (PORTAbits.RA1)

#define 	BUTTON3_TRIS		(TRISBbits.TRISB2)
#define 	BUTTON3             (PORTBbits.RB2)

// end stop sensors
#define 	ENDSTOP_LOW_TRIS		(TRISBbits.TRISB14)
#define 	ENDSTOP_LOW             (PORTBbits.RB14)
        
#define 	ENDSTOP_HIGH_TRIS		(TRISBbits.TRISB13)
#define 	ENDSTOP_HIGH            (PORTBbits.RB13)

#define BAUDRATE_UART2      115200UL
//// for PBCLOCK 40MHz
#define BRG_DIV_UART2           4   // this is NOT the baud rate register value!
#define BRGH_UART2              1

#define BAUDRATE_UART1      9600UL
//// for PBCLOCK 40MHz
#define BRG_DIV_UART1           16   // this is NOT the baud rate register value!
#define BRGH_UART1              0


//// for PBCLOCK 48MHz
//#define BRG_DIV_UART2           16  // this is NOT the baud rate register value!    
//#define BRGH_UART2               0


#define DEBUG_puts      UART2PrintString




#endif // #ifndef HARDWARE_PROFILE_H

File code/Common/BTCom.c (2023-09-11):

// BLE protocol handling module
// (C) 2023-09-09 by Daniel Porzig

#include "BTCom.h"
#include "UART1.h"


#define MAX_PACKET_SIZE         256

#define COMREC_STATE_IDLE       0
#define COMREC_STATE_STARTSEQ   1
#define COMREC_STATE_DATADEC    2
#define COMREC_STATE_NEXTISDATA 3

#define COMREC_DECODE_DONE              1       // decoding done
#define COMREC_ERROR_CHECKSUM           2       // checksum error
#define COMREC_ERROR_MAX_PACKETSIZE     3       // max. packet size exceeded
#define COMREC_ERROR_TIMEOUT            4       // timeout occured before complete package was received
#define COMREC_ERROR_SYNTAX             5       // syntax error, unexpected data received

//Communications Control bytes
#define STX             0x55
#define ETX             0x04
#define DLE             0x05


#define TIMEOUT_CNT     500     // approx 2 second counter    


#define _VERBOSE_



WORD responseBytes;                                                                 //Number of bytes in command response
BYTE buffer[MAX_PACKET_SIZE+1];                                                     //Transmit/Recieve Buffer
BYTE checksum;
WORD dataCount;

BYTE comRecState = 0;       // status of command receiver
WORD comRecTimeout = TIMEOUT_CNT;   

CommandStruct BTcoms[BTCOM_MAX_NUMBER_COMMANDS];
BYTE numComsUsed;


static char txt[60];


static void SendFWStringBT(BYTE *outbuf, WORD *len);
void BTCom_defaultCallback(BYTE *buf_in, BYTE *buf_out, BYTE* len);

// initialize protocol handler
void BTCom_Init()
{
    BYTE i;
    checksum = 0;
    dataCount = 0;
    comRecState = 0;
    
    for(i=0; i<BTCOM_MAX_NUMBER_COMMANDS; i++)
    {
        BTcoms[i].CmdID = 0xFF;
        BTcoms[i].callback = NULL;
    }
    numComsUsed = 0;
}

// add a command including callback to protocol handler
void BTCom_addCallback(BYTE CmdID, VoidFnctCallback callback)
{
    if(numComsUsed == BTCOM_MAX_NUMBER_COMMANDS)
        return;
    
    BTcoms[numComsUsed].CmdID = CmdID;
    BTcoms[numComsUsed].callback = callback;
    numComsUsed++;
}

// protocol handler task
BYTE BTCom_Task()
{
    BYTE RXByte;
    BYTE status = 0;
    

    // check user inputs
    while(!UART1_BufIsEmpty())
    {
        RXByte=UART1_BufRead();
        comRecTimeout = TIMEOUT_CNT; // reset timeout counter
  
        
//        sprintf(txt,"%02X,",RXByte);
//        UART3PrintString(txt);        
        
        switch(comRecState)
        {
            case COMREC_STATE_IDLE:     // Idle
                
                if(RXByte == STX)
                {
                    // first STX received, wait for second STX
                    comRecState = COMREC_STATE_STARTSEQ;

                }
                else
                {
                    //status = COMREC_ERROR_SYNTAX;   // error, unexpected data received
                    ;       // unexpected data received, ignore.
                }

            break;
            case COMREC_STATE_STARTSEQ:     // active sequence, first STX received, wait for second STX

                if(RXByte == STX)
                {
                    // second STX received, following bytes are data
                    comRecState = COMREC_STATE_DATADEC;

                    dataCount = 0;
                    checksum = 0;
                    
                    // DEBUG: start sequence
#ifdef _VERBOSE_
                    DEBUG_puts("\r\n<[");
#endif
                }
                else
                {
                    status = COMREC_ERROR_SYNTAX;   // error, unexpected data received
                }
                
            break;
            case COMREC_STATE_DATADEC:     // active sequence, store incoming data into buffer
                
				switch(RXByte)
                {
					case STX: //Start over if STX
						checksum = 0;
						dataCount = 0;
                        
                        // DEBUG: start sequence
#ifdef _VERBOSE_                        
                        DEBUG_puts("\r\n<[");                        
#endif
                    break;

					case ETX: //End of packet if ETX
                        
                        //Test checksum
						checksum = ~checksum + 1;                                   
						                        
						if(checksum == 0) 
                        {
                            // checksum okay, continue with Command Decoding
                            status = COMREC_DECODE_DONE;
#ifdef _VERBOSE_                            
                            DEBUG_puts("] OK\n\r");
#endif                            
                        }
                        else
                        {
                            // checksum error.
                            status = COMREC_ERROR_CHECKSUM;
                            dataCount = 0xFFFF;                                         //Otherwise restart                            
                            
                            
                        }
					break;

					case DLE: //If DLE, treat next as data
                        
                        // signal receiver state machine that next byte is
                        // to be treated as data
                        comRecState = COMREC_STATE_NEXTISDATA;
                        
                    break;
					default: // regular data byte
						checksum += RXByte;
						buffer[dataCount++] = RXByte;

#ifdef _VERBOSE_                        
                        sprintf(txt,"%02X",RXByte);
                        DEBUG_puts(txt);
#endif
                        
                        if(dataCount <= MAX_PACKET_SIZE+1)
                        {
                            ; // everything ok
                        }
                        else
                        {
                            // max. packet size exceeded
                            status = COMREC_ERROR_MAX_PACKETSIZE;
                        }
					break;        
                }
                
            break;
            case COMREC_STATE_NEXTISDATA:     // active sequence, treat current byte as data without inspection
                
                // treat as regular data byte
                checksum += RXByte;
                buffer[dataCount++] = RXByte;
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

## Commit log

2023-07-17 Create CAD
2023-07-17 initial upload
    [FilterClamp.STL, FlatCap.STL, MagnetCarrierLong.STL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]
2023-09-08 PCB design files updated
    [AutoDuctMainboard_v1.1.brd, AutoDuctMainboard_v1.1.sch, BluetoothAdapter_v2.brd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]
2023-09-08 Gerber files added

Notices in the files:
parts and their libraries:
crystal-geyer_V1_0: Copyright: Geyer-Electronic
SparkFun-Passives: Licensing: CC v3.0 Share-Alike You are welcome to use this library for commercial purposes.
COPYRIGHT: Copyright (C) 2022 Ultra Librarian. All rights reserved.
